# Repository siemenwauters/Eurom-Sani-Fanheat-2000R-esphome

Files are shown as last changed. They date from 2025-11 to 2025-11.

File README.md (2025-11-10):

To give the bathroom that extra boost in temperature when the woman of the house gets ready i needed a smart controlled heater that i could control from home assistant. 
Quickly it became clear that there is not really any decent wall heaters that have a wifi intergration other than some that use some non standard version of tuya.

Since those already cost a lot more just to add the wifi functionality to the heater i went on a path to build my own. The first attempt with a ir led to control a heater worked but was not relyable enough to my teste.
When i found a little heater that comes from a decent brand on a local second hand site i jumped for the opportunity to get it at 15 euro since i did not need the warranty anyway with my modifications.

Below is a picture of the end result



if you want to replicate this project you might have to do a little work of your own but i can give you the bulk of the needed information.

When you open the heater ( there is also 2 screws underneath the 2 rubber feet on the wall standoffs ) you will find that the electronics consist of 2 boards. 
The board in the front that handles logic , IR receiver status indication etc. The other board controls the relays and the fan.

The good news is that the interface between these 2 boards is so simple that we can simply replace the complete control module with the esp32 and a relay board ( you could use something else, relays are just simple to keep things separated ). make sure to keep the screws since i used those to mount my relay and esp board.

The parts i used are these: ( you can use other variations i will add some info why i picked these )
relay board : https://nl.aliexpress.com/item/1005003571799820.html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 ( needed a board that worked with the esp 3.3V )
ESP32C6 : i got the esp32c6 since i got these when i wanted to try and make a zigbee device. this was not simple enough compared to esphome so i switched halfway trough the project. Another esp will work as long as you change the pins but the antenna connector is usefull.
PCB's : https://nl.aliexpress.com/item/1005008177952205.html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 i got the 4x6 ones. i had to make the holes a bit larger anyway so any board will work with some changes.
usb module: https://nl.aliexpress.com/item/1005009204958739.html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 i received a comment that this module is not relyable so use it at your own risk. it is just what i used but anything that is compact and can provide the esp with power will work.

other than that i got a 2.4ghz antenna, some headers, some cables general purpose stuff basically. 

I added a verry basic wiring diagram that hopefully shows the idea. 

How this works:
- the control board wants eather ground or 5v on the control pins. By connecting the ground and 5v leads to all relays we can us the common relay pin as the output that is eather ground or 5v.
- The code controls these 3 outputs like it would when using the remote but adds the advantage of wifi control. Currently since i removed the ir receiver this function is no longer working. if you want ir controll you can just add it in by adding a ir receiver and listen for the codes and then add them to the esphome yaml.
- the temperature sensor is usefull to measure the temperature in the room and it is used to run the auto mode. If you do not have a temperature sensor i would suggest to remove all references to the auto mode.

what works :
- fan mode
- heater 1
- both heaters
- auto mode ( crude code with a simple hysteresis to stay around 23 degrees )

The fan will always run for 30 seconds after the heater is turned off to cool down the heater. if you dont want this change the comparator of 60 to 0.
the heater can only run for 60 minutes in the modes where the heaters are turned off. this is so you do not leave it on indefinately and dont need to handle it in home assistant. (look for 7200)

the interval runs every 500ms that is why the counts are double the amount of seconds.

to get a 230v connection on the control board i just soldered the wires to the blue and red ( N and L ) connections on the board. You might be able to power the esp from the 5v line but i have no idea how much current this can handle. 

The sensor gets put in the original sensor's hole in the back and is attached with some hot glue and a 3d printed spacer. 




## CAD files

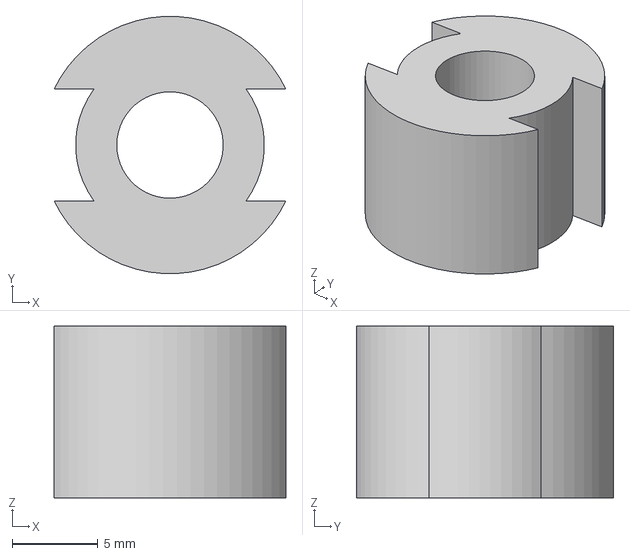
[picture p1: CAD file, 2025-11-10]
Spacer.step
13.5 x 15.0 x 10.0 mm

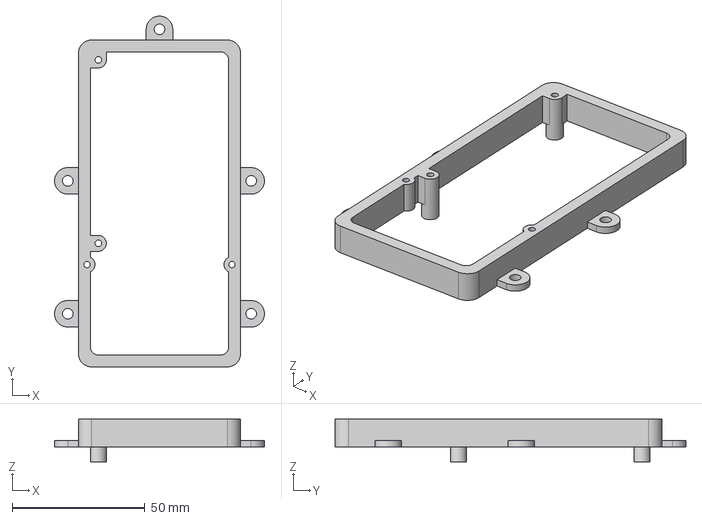
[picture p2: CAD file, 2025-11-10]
Frame.step
79.0 x 132.0 x 16.0 mm

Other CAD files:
Controller frame.3mf
Sensor spacer.3mf
